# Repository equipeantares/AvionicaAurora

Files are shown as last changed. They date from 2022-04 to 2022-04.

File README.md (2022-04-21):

# Icaro-I (Aviônica Aurora V1.0)

## Introdução 

### Motivação

A equipe Antares de espaçomodelismo da Unicamp tem como um de seus projetos desenvolvidos o foguete Aurora. Trata-se de um foguete de propulsão sólida com apogeu esperado de 1km. Como parte dos requisitos necessários para ter sucesso na missão, o foguete precisa de um sistema de aviônica que será responsável por coletar dados e tomar decisões previamente programadas durante o voo. 

### Objetivo

Sendo assim, o objetivo deste projeto é desenvolver um sistema de aviônica capaz de detectar o apogeu programado e acionar o sistema de recuperação. Deve também ser capaz de transmitir os dados de voo ao solo em tempo real e coletar informações sobre a posição do foguete, possibilitando sua localização após aterrisagem. Além disso, deve ser dimensionada para caber na estrutura interna do foguete.

### Soluções comerciais

Pelo fato de o sistema precisar ser personalizado, se ajustando ao sistema presente no foguete e aos demais requisitos específicos do projeto, não existem alternativas comerciais que cumpram integralmente o objetivo.

## Especificação
    - Microcontrolador: o dispositivo deverá ser capaz de fazer processamentos lógicos, sendo assim necessário um microcontrolador. Por motivos de acessibilidade e familiaridade, será utilizada a plataforma Arduino no MCU ESP-8266 12F.

    - Comunicação e dados: com o objetivo de enviar dados de telemetria do foguete, o dispositivo deverá ter um sistema transceptor, que será implementado por um módulo LoRA E32-915T20D. Além disso, contará com uma interface para cartão MicroSD, possibilitando que os dados brutos sejam armazenados para uma análise mais precisa posterior.

    - Interface: como interface, o dispositivo contará com conectores para alimentação externa, além de pinos seletores, que selecionam, principalmente, se o sistema é o principal ou uma redundância e se o acionamento será interno ou externo (para testes).

    - Ignição: a aviônica precisa implementar um sistema de ignição que será o responsável pela liberação da recuperação.

    - Alimentação: o sistema tem interface de alimentação externa.

    - Redundância: o dispositivo implementa solução para um sistema com redundância nos subsistemas críticos, provendo maior segurança.

    - Localização: a fim de garantir que seja possível localizar o foguete após o pouso, o sistema deve ser capaz de transmitir a posição em tempo real por meio de um sistema GPS e de emitir um aviso sonoro por meio de um buzzer.

    - Detecção de apogeu: para ser capaz de detectar o momento do apogeu, a aviônica deve implementar um altímetro.

## Pinagem

### Pinout conector Screw bateria 18650

Pino | Sinal
-----|------
1  | VBat
2  | GND

### Pinout conector Screw do Acionamento

Pino | Sinal
-----|------
  1  | NiCr_ISO
  2  | GND_ISO

### Pinout conector Screw da Redundancia

Pino | Sinal
-----|------
  1  | Redundancy_IN
  2  | Redundancy_OUT

### Pinout conector Seleção Redundância

Pino | Sinal
-----|------
  1  | Redundancy_OUT
  2  | IGN
  3  | Main_IGN

### Pinout conector Transistor PNP acionamento (interno)

Pino | Sinal
-----|------
  1  | Emissor
  2  | Coletor

### Pinout conector Optoacoplador acionamento (externo)

Pino | Sinal
-----|------
  1  | Coletor
  2  | Emissor

## Testes

    A fim de garantir que o sistema seja seguro e que tudo funcione como esperado, é necessário realizar testes controlados de cada parte do sistema, tentando antecipar possíveis falhas que possam ocorrer. 
    Como o sistema de ignição não pode ter acionamento indesejado, devem ocorrer testes em ambientes adversos, como, por exemplo, com componentes desconectados, e o resultado esperado é que o sistema não ative em nenhuma dessas situações.
    Além disso, todos os sensores presentes devem ser validados.

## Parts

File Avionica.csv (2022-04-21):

Source: | /home/gustavo/Área de Trabalho/Unicamp/Antares/KiCad/teste/Avionica/Avionica.sch
Date: | Sáb 16 Abr 2022 23:51:37 -03
Tool: | Eeschema 5.1.12-84ad8e8a86~92~ubuntu16.04.1
Generator: | /usr/share/kicad/plugins/bom_csv_grouped_by_value_with_fp.py
Component Count: | 41
Ref | Qnty | Value | Cmp name | Footprint | Description | Vendor
A1, | 1 | BMP280_Module | BMP280_Module | CharlesLabs:BMP280_Module |  | https://www.filipeflop.com/produto/sensor-de-pressao-e-temperatura-bmp280/
A2, | 1 | SD_Card_Module | SD_Card_Module | CharlesLabs:SD_Card_Module |  | https://www.usinainfo.com.br/outros-modulos-arduino/mini-sd-card-arduino-mini-leitor-micro-sd-card-5051.html
BT1, | 1 | Battery_Cell | Battery_Cell | Battery:BatteryHolder_Keystone_1042_1x18650 | Single-cell battery
BZ1, | 1 | Buzzer | Buzzer | Buzzer_Beeper:Buzzer_12x9.5RM7.6 | Buzzer, polarized | https://lcsc.com/product-detail/Buzzers_Jiangsu-Huaneng-Elec-TMB12A05_C96093.html
C1, | 1 | 100n | C_Small | Capacitor_SMD:C_0805_2012Metric | Unpolarized capacitor, small symbol
C2, C3, | 2 | 10u | C_Small | Capacitor_SMD:C_0805_2012Metric | Unpolarized capacitor, small symbol
D1, | 1 | Green | LED_Small | LED_THT:LED_D3.0mm_Horizontal_O1.27mm_Z2.0mm | Light emitting diode, small symbol
D2, | 1 | Red | LED_Small | LED_THT:LED_D3.0mm_Horizontal_O1.27mm_Z2.0mm | Light emitting diode, small symbol
D3, | 1 | 1N4148 | D_Small | Diode_SMD:D_SOD-123 | Diode, small symbol
F1, | 1 | Polyfuse_Small | Polyfuse_Small | Fuse:Fuse_1206_3216Metric_Castellated | Resettable fuse, polymeric positive temperature coefficient, small symbol
F2, | 1 | Fuse | Fuse | Fuse:Fuseholder_Cylinder-5x20mm_Stelvio-Kontek_PTF78_Horizontal_Open | Fuse
J1, J2, J3, J6, J9, | 5 | Screw_Terminal_01x02 | Screw_Terminal_01x02 | TerminalBlock_Phoenix:TerminalBlock_Phoenix_MKDS-1,5-2_1x02_P5.00mm_Horizontal | Generic screw terminal, single row, 01x02, script generated (kicad-library-utils/schlib/autogen/connector/)
J4, J5, | 2 | Header_1x2 | Conn_01x02_Male | Connector_Molex:Molex_KK-254_AE-6410-02A_1x02_P2.54mm_Vertical | Generic connector, single row, 01x02, script generated (kicad-library-utils/schlib/autogen/connector/)
J7, J8, | 2 | Conn_01x03_Male | Conn_01x03_Male | Connector_Molex:Molex_KK-254_AE-6410-03A_1x03_P2.54mm_Vertical | Generic connector, single row, 01x03, script generated (kicad-library-utils/schlib/autogen/connector/)
K1, | 1 | HK4100F-DC3V-SHG | G5V-1 | Relay_THT:Relay_SPDT_Omron_G5V-1 | Ultra-miniature, Highly Sensitive SPDT Relay for Signal Circuits
Q1, | 1 | 2N3906 | 2N3906 | Package_TO_SOT_THT:TO-92_Inline | -0.2A Ic, -40V Vce, Small Signal PNP Transistor, TO-92
Q2, | 1 | PN2222A | PN2222A | Package_TO_SOT_THT:TO-92_Inline | 1A Ic, 40V Vce, NPN Transistor, General Purpose Transistor, TO-92
R1, R4, | 2 | 1M | R_Small | Resistor_SMD:R_0805_2012Metric | Resistor, small symbol
R2, | 1 | 100 | R_Small | Resistor_SMD:R_0805_2012Metric | Resistor, small symbol
R3, | 1 | 0 | R_Small | Resistor_SMD:R_0805_2012Metric | Resistor, small symbol
R5, | 1 | 125 | R_Small | Resistor_SMD:R_0805_2012Metric | Resistor, small symbol
R6, | 1 | 75 | R_Small | Resistor_SMD:R_0805_2012Metric | Resistor, small symbol
R7, | 1 | 3.3K | R_Small | Resistor_SMD:R_0805_2012Metric | Resistor, small symbol
R8, R9, | 2 | 4.7K | R_Small | Resistor_SMD:R_0805_2012Metric | Resistor, small symbol
R10, | 1 | 330 | R_Small | Resistor_SMD:R_0805_2012Metric | Resistor, small symbol
R11, | 1 | 10K | R_Small | Resistor_SMD:R_0805_2012Metric | Resistor, small symbol
U1, | 1 | GY-NEO6MV2 | GY-NEO6MV2 | GPS:GY-NEO6MV2 |  | https://www.robocore.net/sensor-robo/modulo-gps-gy-neo6mv2-com-antena
U2, | 1 | ME6217C33M5G | ME6217C33M5G-BaseAurora | Package_TO_SOT_SMD:SOT-23-5
U3, | 1 | 74AHC1G02 | 74AHC1G02 | Package_TO_SOT_SMD:SOT-23-5 | Single NOR Gate, Low-Voltage CMOS
U4, | 1 | 4N32M | 4N25 | Package_DIP:DIP-6_W7.62mm | DC Optocoupler Base Connected, Vce 30V, CTR 20%, Viso 2500V, DIP6
U5, | 1 | NodeMCU1.0(ESP-12E) | NodeMCU1.0(ESP-12E) | ESP8266:ESP12F-Devkit-V3
U6, | 1 | E32-915T20D | E32-915T20D | LoRA:E32-xxxT20D

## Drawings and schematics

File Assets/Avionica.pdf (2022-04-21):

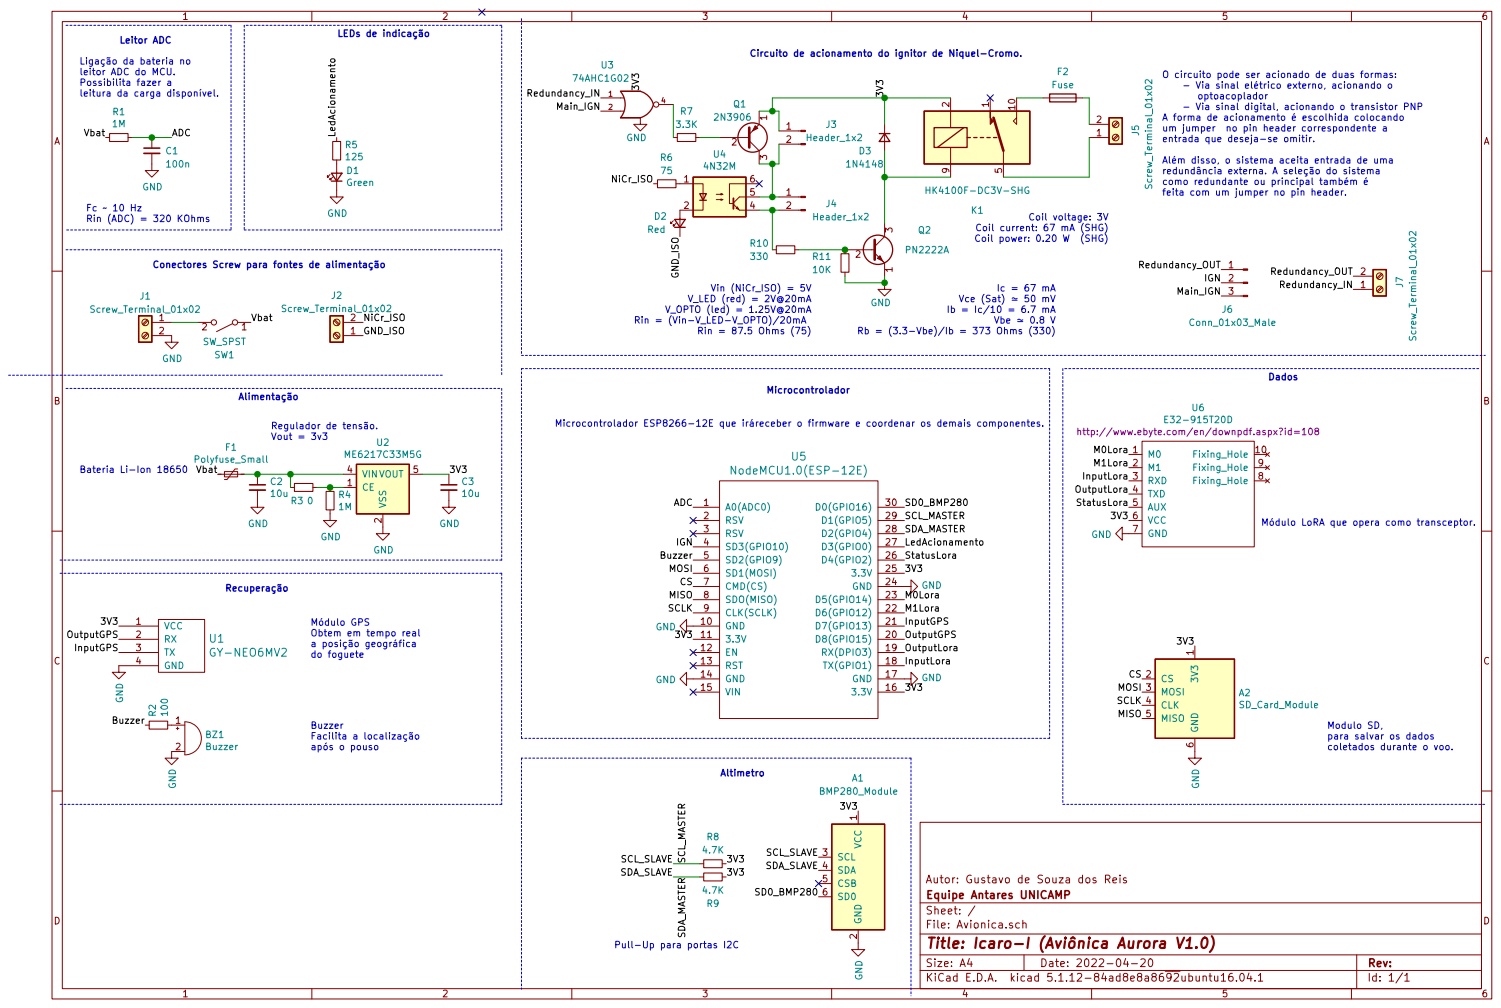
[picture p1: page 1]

Circuito de acionamento do ignitor de Niquel-Cromo. Leitor ADC

Ligação da bateria no
leitor ADC do MCU. Possibilita fazer a
leitura da carga disponível.

- Via sinal elétrico externo, acionando o
optoacoplador
- Via sinal digital, acionando o transistor PNP
A forma de acionamento é escolhida colocando um jumper no pin header correspondente a

entrada que deseja-se omitir. Além disso, o sistema aceita entrada de uma

redundância externa. A seleção do sistema
como redundante ou principal também é
feita com um jumper no pin header.

Regulador de tensão. Vout = 3v3 Fc 10 Hz Rin (ADC) = 320 KOhms

Coil current: 67 mA (SHG)
Coil power: 0.20 W (SHG)

Conectores Screw para fontes de alimentação

Microcontrolador ESP8266-12E que iráreceber o firmware e coordenar os demais componentes.

Módulo LoRA que opera como transceptor.

após o pouso Módulo GPS Obtem em tempo real

1 CS 2 MOSI 3 CLK 4 MISO 5 GND
SCLK MOSI CS

Autor: Gustavo de Souza dos Reis
Id: 1/1 Title: Icaro-I (Aviônica Aurora V1.0) File: Avionica.sch Sheet: / Equipe Antares UNICAMP

Pull-Up para portas I2C

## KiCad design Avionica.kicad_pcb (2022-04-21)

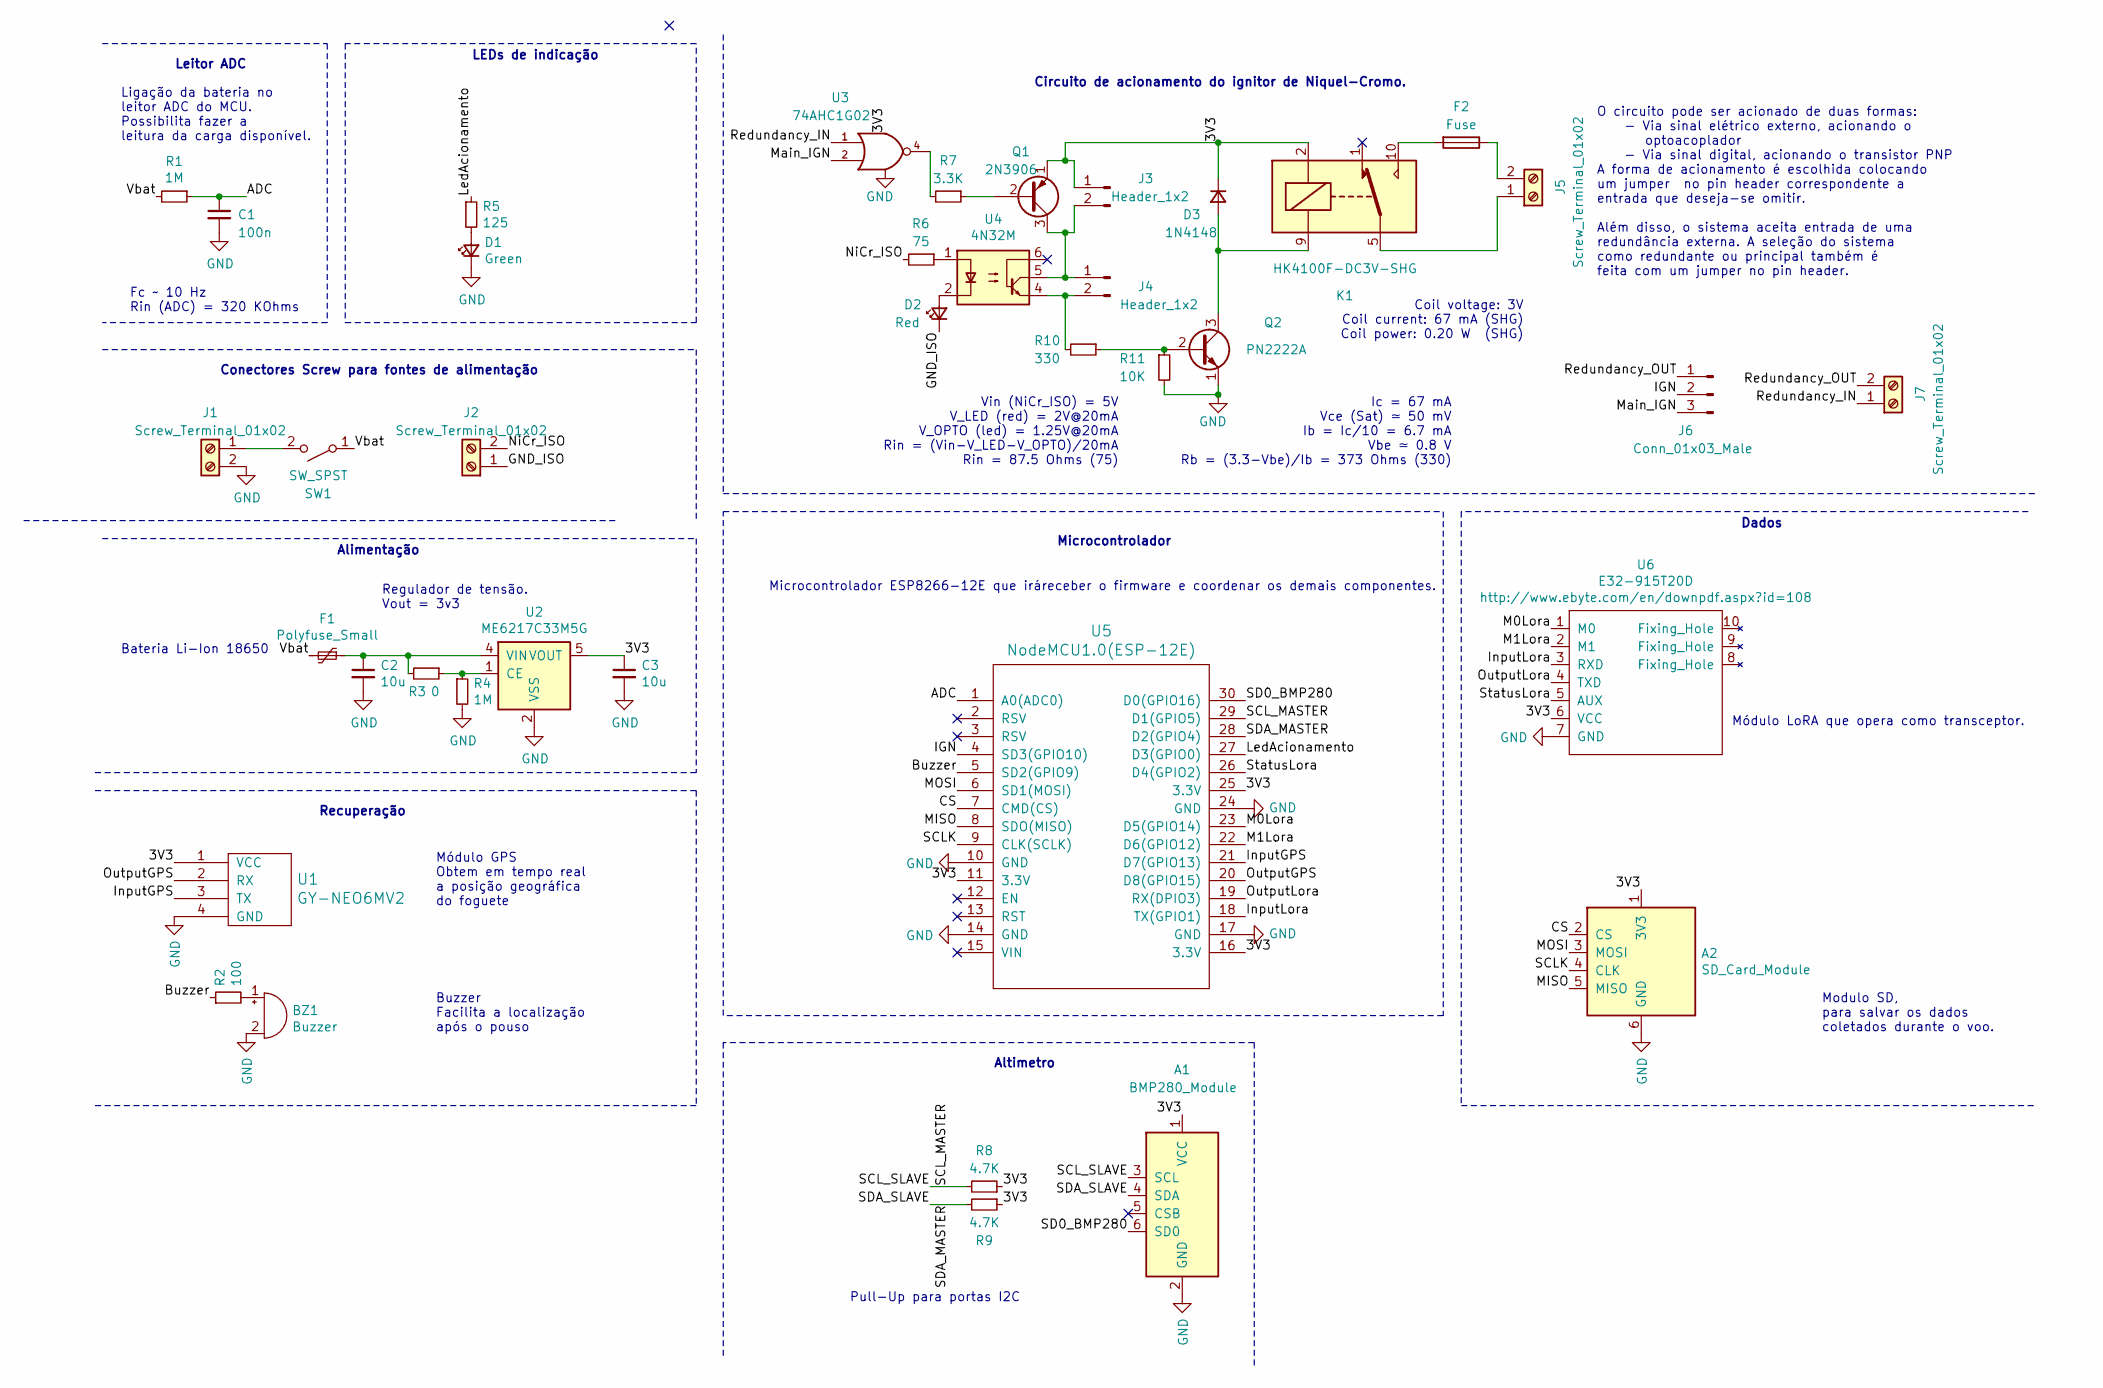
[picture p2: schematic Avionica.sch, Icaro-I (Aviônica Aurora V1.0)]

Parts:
A1: BMP280_Module
A2: SD_Card_Module
BZ1: Buzzer; Buzzer_12x9.5RM7.6
C1: 100n; C_0805_2012Metric
C2, C3: 10u; C_0805_2012Metric
D1: Green; LED_D3.0mm
D2: Red; LED_D3.0mm
D3: 1N4148; D_SOD-123
F1: Polyfuse_Small; Fuse_1206_3216Metric_Castellated
F2: Fuse; Fuseholder_Cylinder-5x20mm_Stelvio-Kontek_PTF78_Horizontal_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
J1, J2, J5, J7: Screw_Terminal_01x02; TerminalBlock_Phoenix_MKDS-1,5-2_1x02_P5.00mm_Horizontal
J3, J4: Header_1x2; Molex_KK-254_AE-6410-02A_1x02_P2.54mm_Vertical
J6: Conn_01x03_Male; Molex_KK-254_AE-6410-03A_1x03_P2.54mm_Vertical
K1: HK4100F-DC3V-SHG; Relay_SPDT_Omron_G5V-1
Q1: 2N3906; TO-92_Inline
Q2: PN2222A; TO-92_Inline
R1, R4: 1M; R_0805_2012Metric
R2: 100; R_0805_2012Metric
R3: 0; R_0805_2012Metric
R5: 125; R_0805_2012Metric
R6: 75; R_0805_2012Metric
R7: 3.3K; R_0805_2012Metric
R8, R9: 4.7K; R_0805_2012Metric
R10: 330; R_0805_2012Metric
R11: 10K; R_0805_2012Metric
SW1: SW_SPST; Screw_Switch
U1: GY-NEO6MV2
U2: ME6217C33M5G; SOT-23-5
U3: 74AHC1G02; SOT-23-5
U4: 4N32M; DIP-6_W7.62mm
U5: NodeMCU1.0(ESP-12E); ESP12F-Devkit-V3
U6: E32-915T20D; E32-xxxT20D

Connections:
/ADC: C1.1, R1.1, U5.1 (A0(ADC0))
/Buzzer: R2.1, U5.5 (SD2(GPIO9))
/CS: A2.2 (CS), U5.7 (CMD(CS))
/GND_ISO: D2.1 (K), J2.1
/IGN: J6.2, U5.4 (SD3(GPIO10))
/InputGPS: U1.3 (TX), U5.21 (D7(GPIO13))
/InputLora: U5.18 (TX(GPIO1)), U6.3 (RXD)
/LedAcionamento: R5.1, U5.27 (D3(GPIO0))
/M0Lora: U5.23 (D5(GPIO14)), U6.1 (M0)
/M1Lora: U5.22 (D6(GPIO12)), U6.2 (M1)
/MISO: A2.5 (MISO), U5.8 (SDO(MISO))
/MOSI: A2.3 (MOSI), U5.6 (SD1(MOSI))
/Main_IGN: J6.3, U3.2
/NiCr_ISO: J2.2, R6.2
/OutputGPS: U1.2 (RX), U5.20 (D8(GPIO15))
/OutputLora: U5.19 (RX(DPIO3)), U6.4 (TXD)
/Redundancy_IN: J7.1, U3.1
/Redundancy_OUT: J6.1, J7.2
/SCLK: A2.4 (CLK), U5.9 (CLK(SCLK))
/SCL_MASTER: A1.3 (SCL), R8.2, U5.29 (D1(GPIO5))
/SD0_BMP280: A1.6 (SD0), U5.30 (D0(GPIO16))
/SDA_MASTER: A1.4 (SDA), R9.2, U5.28 (D2(GPIO4))
/StatusLora: U5.26 (D4(GPIO2)), U6.5 (AUX)
/Vbat: F1.2, R1.2, SW1.1 (A)
GND: A1.2 (GND), A2.6 (GND), BZ1.2 (+), C1.2, C2.2, C3.2, D1.1 (K), J1.2, Q2.1 (E), R4.2, R11.2, U1.4 (GND), U2.2 (VSS), U3.3 (GND), U5.10 (GND), U5.14 (GND), U5.17 (GND), U5.24 (GND), U6.7 (GND)
unnamed: BZ1.1 (-), R2.2
unnamed: C2.1, F1.1, R3.2, U2.4 (VIN)
unnamed: D1.2 (A), R5.2
unnamed: D2.2 (A), U4.2
unnamed: D3.2 (A), K1.9, Q2.3 (C)
unnamed: F2.1, J5.2
unnamed: F2.2, K1.10
unnamed: J1.1, SW1.2 (B)
unnamed: J3.2, J4.1, Q1.3 (C), U4.5
unnamed: J4.2, R10.2, U4.4
unnamed: J5.1, K1.5, K1.6
unnamed: Q1.2 (B), R7.1
unnamed: Q2.2 (B), R10.1, R11.1
unnamed: R3.1, R4.1, U2.1 (CE)
unnamed: R6.1, U4.1
unnamed: R7.2, U3.4
VCC: A1.1 (VCC), A2.1 (3V3), C3.1, D3.1 (K), J3.1, K1.2, Q1.1 (E), R8.1, R9.1, U1.1 (VCC), U2.5 (VOUT), U3.5 (VCC), U5.11 (3.3V), U5.16 (3.3V), U5.25 (3.3V), U6.6 (VCC)

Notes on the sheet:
Coil voltage: 3V Coil current: 67 mA (SHG) Coil power: 0.20 W (SHG)
Fc ~~ 10 Hz Rin (ADC) = 320 KOhms
Regulador de tensão. Vout = 3v3
Conectores Screw para fontes de alimentação
LEDs de indicação
Ligação da bateria no leitor ADC do MCU. Possibilita fazer a leitura da carga disponível.
Módulo LoRA que opera como transceptor.
Microcontrolador ESP8266-12E que iráreceber o firmware e coordenar os demais componentes.
O circuito pode ser acionado de duas formas: - Via sinal elétrico externo, acionando o optoacoplador - Via sinal digital, acionando o transistor PNP A forma de acionamento é escolhida colocando um jumper no pin header correspondente a entrada que deseja-se omitir. Além disso, o sistema aceita entra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
Microcontrolador
Dados
Bateria Li-Ion 18650
Alimentação
Leitor ADC
Circuito de acionamento do ignitor de Niquel-Cromo.
Ic = 67 mA Vce (Sat) ≃ 50 mV Ib = Ic/10 = 6.7 mA Vbe ≃ 0.8 V Rb = (3.3-Vbe)/Ib = 373 Ohms (330)
Vin (NiCr_ISO) = 5V V_LED (red) = 2V@20mA V_OPTO (led) = 1.25V@20mA Rin = (Vin-V_LED-V_OPTO)/20mA Rin = 87.5 Ohms (75)
Recuperação
Altimetro
Pull-Up para portas I2C
Modulo SD, para salvar os dados coletados durante o voo.
Módulo GPS Obtem em tempo real a posição geográfica do foguete
Buzzer Facilita a localização após o pouso

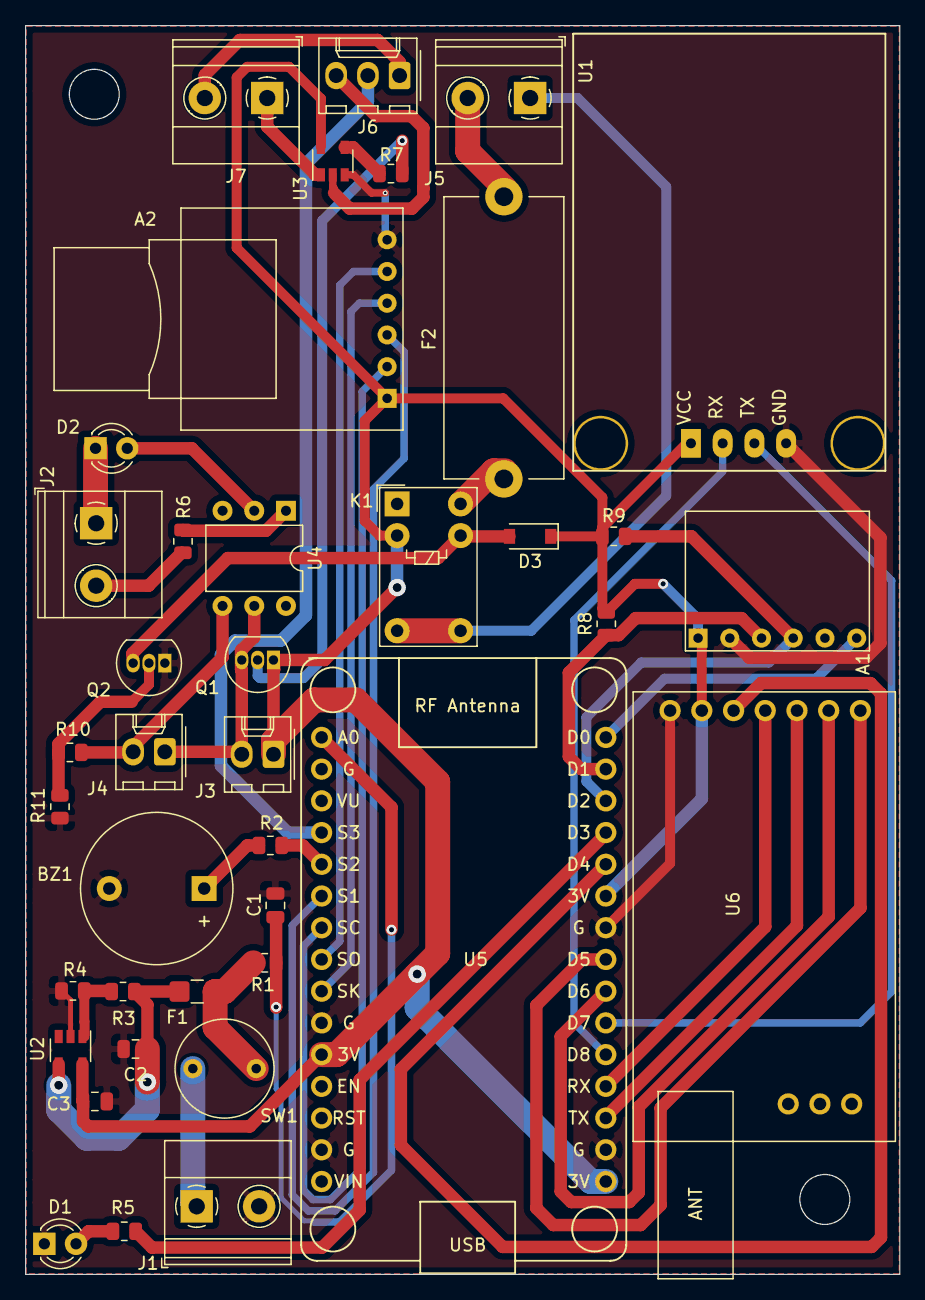
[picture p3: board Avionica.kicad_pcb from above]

Board: 2 copper layers, 70.0 x 100.0 mm, 39 parts (0 on the bottom side), 42 nets.
